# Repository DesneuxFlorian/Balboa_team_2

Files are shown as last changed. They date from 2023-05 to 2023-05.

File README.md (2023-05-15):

# Balboa_team_2
Advanced control 2 balboa robot
As part of the Advanced control 2 course, we did a job in which we were able to choose our own subject with the mobile balboa robot. We opted for subject number 6 "SLAM ROBOT". This subject consists in creating a map of an unknown environment thanks to the remote control of our laptop. The purpose of this documentation is to understand how to reproduce our project and then improve it for the years to come.

Vidéo to project: https://www.youtube.com/watch?v=urFcWSqZmxI

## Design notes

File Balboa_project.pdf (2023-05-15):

# 5/15/2023 Advanced control 2:

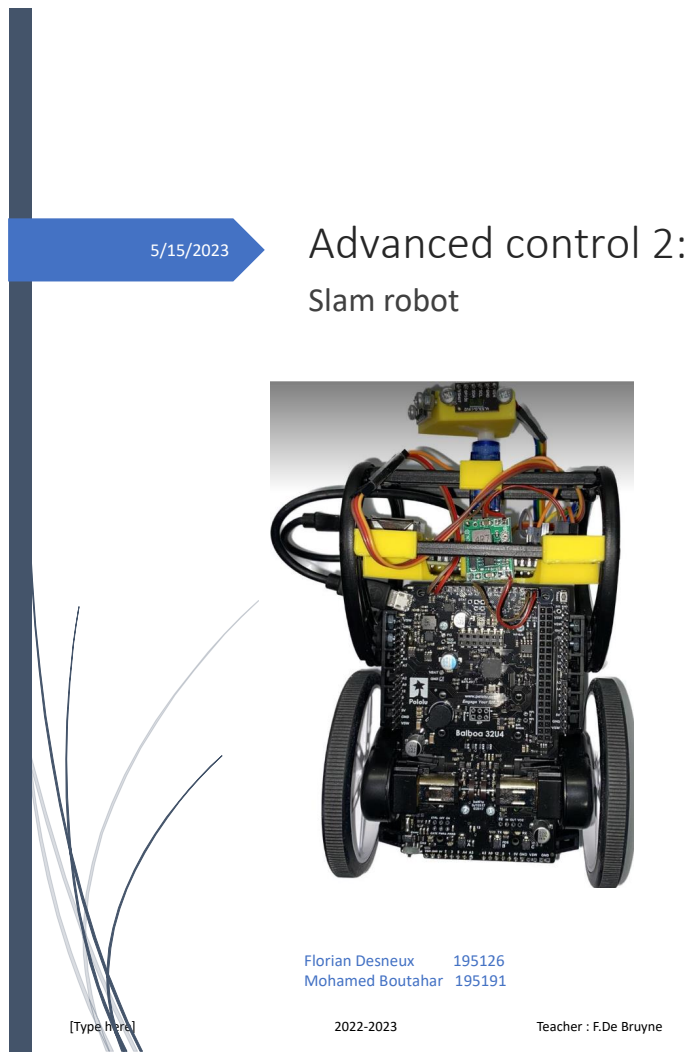
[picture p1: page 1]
[Type here]; Teacher : F.De Bruyne; Slam robot; Florian Desneux; Mohamed Boutahar 195191

## Contents

## 1. Project introduction

As part of the Advanced control 2 course, we did a job in which we were able to choose our own subject with the mobile balboa robot. We opted for subject number 6 "SLAM ROBOT". This subject consists in creating a map of an unknown environment thanks to the remote control of our laptop. The purpose of this documentation is to understand how to reproduce our project and then improve it for the years to come. If you are interested in the details and source files for this project, please follow this link to the project github : https://github.com/DesneuxFlorian/Balboa_team_2

## 2. Objectives

In order to carry out this project as well as possible, we have set ourselves several objectives which are as follows :

- Laser sensor with servo-motor
- Data collected and sended to laptop with mqtt
- Laptop controls the robot with user input
- Basic odometry data computed and sended to the laptop
- Implement a SLAM algorithm

## 3. Raspberry pi Setup

For the project we are using a raspberry pi as the main computer. It will be in charge of the communication between the Balboa and the Laptop. Additionally, the Raspberry will be operating the lidar scanner. We used this approach to try to run a SLAM algorithm on the raspberry.

### 3.1 OS installation

The first step is to install a Linux OS on the raspberry pi. For this we used this tutorial: How to Install Raspberry Pi OS on Your Raspberry Pi. (https://howchoo.com/pi/install-raspberry-pi-os) Because we will want to use remote access to the Raspberry using SSH, we need to add the following step during the installation:

1. Go to additional Settings.
2. Be sure to enable SSH.
3. Put a username and password that you will remember.
4. You can also set the hostname you want, it will become handy later on.
5. Enable and configure your wi-fi settings in the W-lan tab.

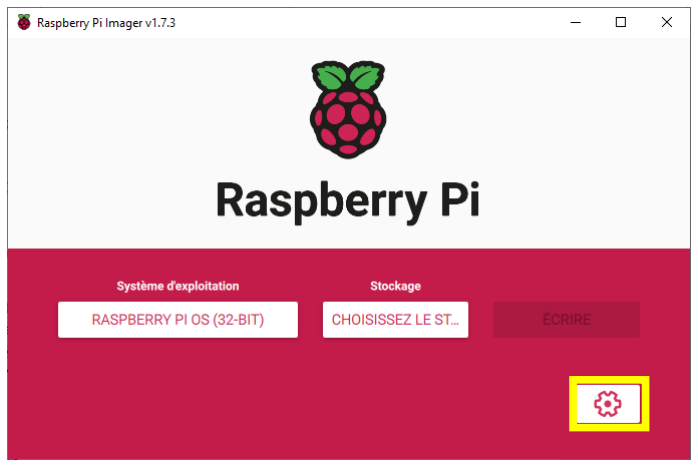
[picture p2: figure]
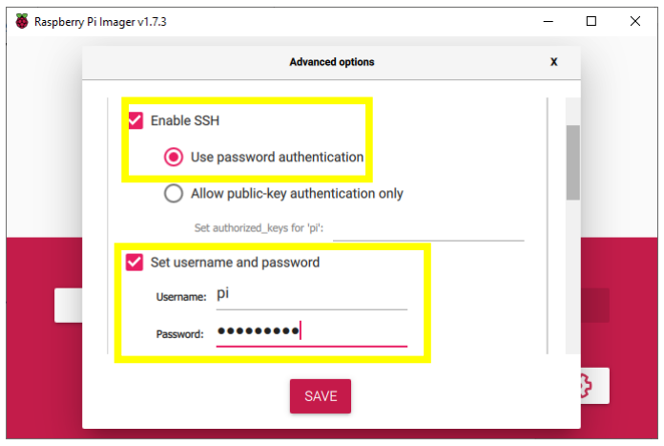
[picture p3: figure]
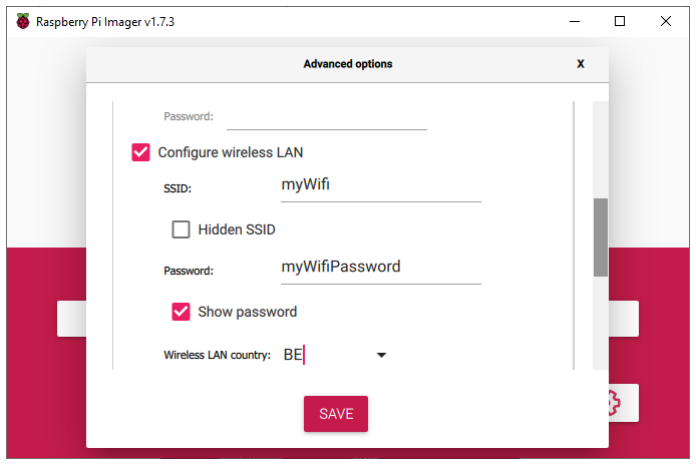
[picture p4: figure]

Save and write the OS to your SD card. You should then be able to boot the raspberry pi.

### 3.2 VNC setup

It is now time to connect via SSH to our raspberry pi. Once that is working, we will install a VNC viewer to access a remote desktop. To access via SSH, we need to know the IP address of the raspberry pi on the current network. To do this, we need to boot the raspberry with the SD card we just configured. When it is done booting (could take a minute or two), we need to find the IP address that has been assigned to the raspberry pi. There are several ways to find the IP address. This tutorial will show different ways to do that: How to Find a Raspberry Pi on a Network. (https://all3dp.com/2/find-raspberry-pi-on-network/) We used the third approach with a windows terminal and using ping command. The hostname of the raspberry pi is the hostname you have configured earlier. You should get an IP address of the type 192.XXX.X.XX. If you get an address with another format, use this one, but you will have to find the IP address once you are connected because VNC viewer only supports the first format.

A second way of finding the IP address remotely is to connect to your router’s login page. Most internet providers allow you to oversee all the connected devices on your network and you should be able to find the IP address of every connected device, including your Raspberry pi. If you cannot find your raspberry pi, it is possible it isn’t connecting properly to your network. Follow the troubleshooting steps of the tutorial to try to find your problem.

We can now test to connect via SSH to the raspberry pi before moving on to the next step. On windows open a command terminal and use the command: ssh pi@192.XXX.X.XX replacing “192.XXX.X.XX” with your raspberry IP address. Enter your password and you should be connected to the raspberry. If you got a IP address of the other type, we need to get the real IP address of the raspberry pi for the VNC viewer. Use the command sudo hostname -I in the command terminal to find it.

You can now install Real VNC (https://www.realvnc.com/fr/connect/download/viewer/) and connect to the pi using it’s IP address. You should get access to the raspberry pi desktop.

### 3.3 MQTT Setup

To communicate with the laptop, our code will use MQTT. So we need to install mosquito on the raspberry pi. We have followed this tutorial enabling remote access without authentication: Install Mosquitto MQTT Broker on Raspberry Pi. (https://randomnerdtutorials.com/how-to-install-mosquitto-broker-on-raspberry-pi/) We also need to install the python package to use mosquito with python. Open a terminal and run pip3 install paho-mqtt.

### 3.4 Additional dependencies Setup

The code is using some other packages. Here is a list of the packages you should install on python3:

− numpy
− serial
− smbus2
− vl53l1x
− json

Install all of these dependencies using PIP3.

Finally you should also go to the configuration tab of the pi and enable i2c, Serial port and VNC. Don’t forget to reboot the pi after changing the configuration (command sudo reboot).

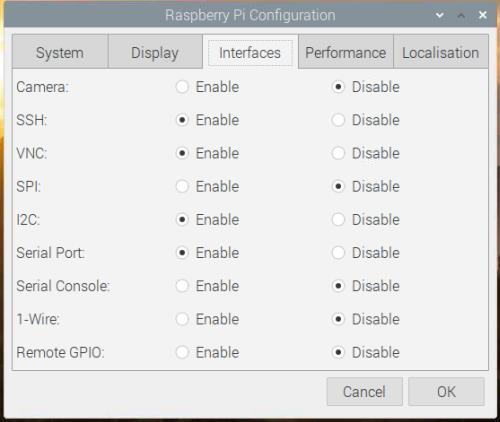
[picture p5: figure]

### 3.5 Hotspot tools V2

We also want to install hotspot tools v2 on our raspberry pi. This way we will be able to control the robot event when there is no available wifi network. The raspberry will boot in a hotspot mode and we then simply need to connect to its local network. This will also enable us to setup new wifi connections without needing to restart the other steps. To install hotspot tools v2 we simply followed the steps for installing from the project Github page¹
| . There is also a video available for a more in depth tutorial.

## 4. Communication between balboa robot and raspberry PI

Here, we will communicate in series between the balboa and the Raspberry PI thanks to a USB cable connecting the balboa robot to one of the USB ports of the Raspberry Pi.

### 4.1 Serial communication

The principle of serial communication is to sequentially send one bit of data at a time from one location to another. For example, using serial data, you can send data from your balboa to a Raspberry Pi or from the Raspberry Pi to the balboa.

After discussing with our teacher, we chose to communicate with a USB cable because it is one of the most common ways to transmit data in serial communications hence the name of universal serial bus. So with balboa, we can easily send and receive data via a USB cable thanks to balboa's built-in serial library.

### 4.2 UART communication

Once the data has arrived on our balboa, it will be stored in what we call "serial reception buffer".

1 https://github.com/km4ack/hotspot-tools2

When bits of data start flowing into the computer, a hardware device in the balboa used for serial communication between two devices called a universal asynchronous receiver/transmitter (UART) assembles each of the 8 bits into a byte. The UART then stores these bytes (up to 64 bytes, in fact) in the serial receive buffer.

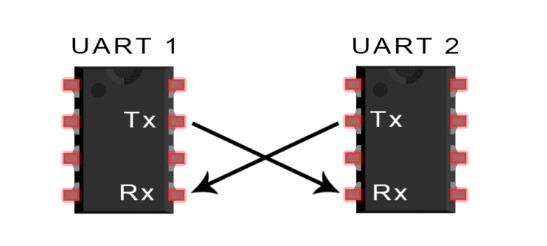
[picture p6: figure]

One wire is for transmitting data (called the TX pin) and the other is for receiving data (called the RX pin). We can only connect two UART devices together.

Once the data is in the serial receive buffer, we can use Serial.read() to read what is in the receive buffer. However, it’s important to understand that it reads in a very specific way. It’ll read out the first available byte from the serial receive buffer and then remove that byte from the buffer.

In order to simplify things, we will impose a rather basic protocol :

- New messages will be read as soon as they arrive
- Messages must not exceed 12 bytes
- Each message will end with a newline character '\n' which we will call our end character

## 5. Communication between Raspberry pi and laptop

We are using 3 different topics for the communication.

1. raspberry/scan
2. raspberry/odom
3. raspberry/setpoint

The first and second topics are published on with the raspberry pi, and the third topic is used to control the balboa from the laptop. It is published on when you press a key controlling the robot. We are using keys “i,j,k,l” to move the robot around, key “t” to start and stop the scanning and finally you can use key “s” to save the data coming from the robot.

## 6. Electrical circuit

Here we will illustrate in detail the wiring of our project

### 6.1 Power supply of the raspberry PI

Regarding the power supply of the raspberry PI, we decided to power it directly with the balboa. The problem is that our raspberry PI has to be powered with 5 V while our balboa provides a battery voltage. To solve this problem, we decided to use a buck converter to reduce this voltage to 5 V. Here is the buck we decided to use:

By using the buck converter, we are sure that there is enough power for the raspberry pi. Normally the balboa already has a 5v bus that we could use, but it was not powerful enough and that’s why we made the choice to use a buck converter.

### 6.2 Servomotor

In order to have a maximum of data to better map the environment, we decided to mount our sensors on a servomotor which will turn it at a certain angle.

### 6.3 Wiring diagrams

Here is a complete assembly of our balboa robot with the different elements such as the buck, the servomotor, the sensors and the raspberry PI

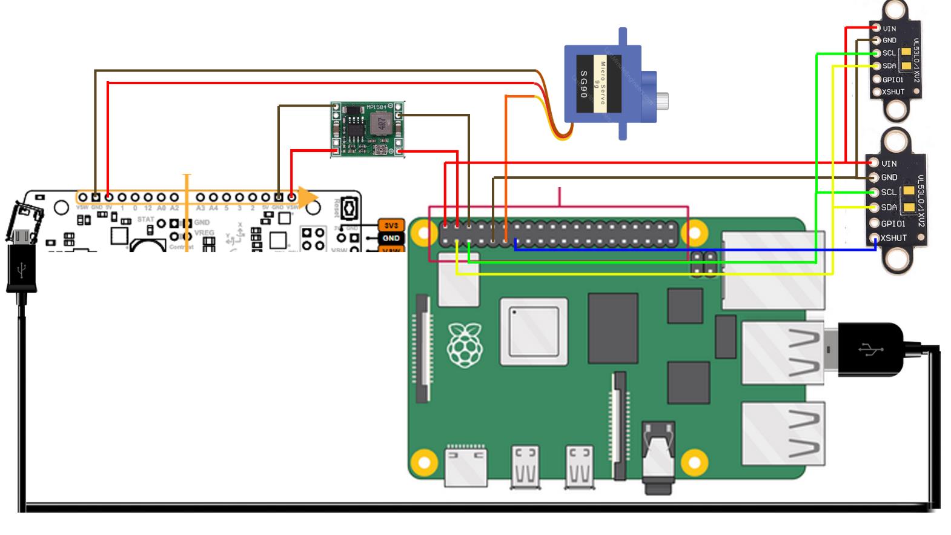
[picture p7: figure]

## 7. Software

The software is composed of three big parts. The first part is the C++ code running on the Balboa robot itself. Basically it is in charge of the control algorithm as well as computing the dead reckoning odometry for the robot. The second part of code is the python code running directly on the raspberry pi. This part of the code is responsible for controlling the lidar scanner, and sending the data to the laptop. It is also used as middleman for controlling the balboa with the laptop. The raspberry pi gets control commands from the laptop trough MQTT, and then sends them to the balboa trough serial. The last part of code is also a python code that is running on the laptop. Its purpose is to retrieve keyboard commands and send them to the raspberry and to receive the scanned data from the raspberry pi and to display them on the screen. It is also in this code that we convert the data from polar to cartesian.

### 7.1 Balboa code

The control is performed by a state-space algorithm. Additionally we have added a few functions:

− ComputeOdom()
− readData()
− treatCommand()
− sendOdometry()

The ComputeOdom function is running every 10ms to evaluate the balboa robot position in a cartesian coordinate system. It is implemented following this article found online²
. The second
and third functions are running at a much higher sampling rate than the rest of the control algorithm. This ensure that a fast serial communication between the raspberry and the balboa as well as a fast handling of the commands. The last function is simply sending the odometry data trough serial when the robot reads a “O” in the serial buffer.

### 7.2 raspberry pi code

The code running on the raspberry pi is composed of 2 files. The Lidar file, that contains a Lidar class. This class is in charge of everything related to the laser scanners. It will connect to the two lidars, then it will start those lidars and finally it has a method to run a scan with the lidars. This class also controls the servo motor on which the two vl53l1x are mounted. The method performing the scan is working this way:

− first it moves the servo to a position
− then it asks the odometry to the Arduino
− get the distance from the two sensors
− appends the angles and distances to a list and performs everything for a new position − finally it returns the lists when the sweep is done

2 Wheel Odometry Model for Differential Drive Robotics (https://medium.com/@nahmed3536/wheel-odometry-model-for-differential-drive-robotics-91b85a012299)

Initially we were not getting the odometry for every point in the scan but only for the last one. It had the advantage to speed up the control of the balboa because it had less communication. But because the slow nature of our scan, it is a lot better to get the odometry for every point so that we can correct the list of angle for every point individually.

The second file is the main file. This file is the one that will be started and running continuously on the raspberry pi. It has a functions that handle the MQTT communication, as well as a main loop running where it will scan around using the lidar object created at the beginning of the code. Before running this file it is important to run the command “sudo pigpiod” in a command terminal so that the lidar class can correctly run. This class is using hardware pwm to control the servo motor. This is so to remove the jitter that we have if we use the conventional software generated pwm.

### 7.3 laptop code

Finally the code running on your laptop is composed of 3 files. The roboviz.py file is a file from the roboviz library written by Simond Levy³
. It has been slightly modified so for better result it is advised to use the file from this project github page. The lidar_to_grid_map.py file is a python file written by Erno Horvath⁴
| . This file has also been modified, thus the file from our github should also
be used to ensure that the code will run. Before running those files you should also check that you have installed the required dependencies on your laptop. For the laptop the dependencies are:
| − numpy − matplotlib − json − paho mqtt − keyboard

## 8. Mechanical assembly

Two 3D printed parts are used to mount the raspberry pi and the servo motor on top of the balboa robot. Those 3d prints simply clip on the already existing mounts. There is also a small 3d printed support to mount the two VL53L1X on the 8g servo motor.

## 9. Results and improvements ideas

The robot is performing quiet well. When it is not scanning around it is easy to drive it around to where we want it to go. But because our scanner is slow we are controlling it with slow values. To start scanning we simply push on “t” on the keyboard. As soon as it starts scanning, there is a noticeable loss of control from the pc. The balboa is less reactive to keyboard commands. This comes from the increased communication from the odometry data. As we drive it around we can slowly see a map displaying on our screen. But because we don’t run a real SLAM algorithm, the map is quickly becoming bad as a result of the odometry drift. The images below show some maps that we could draw.

3 https://github.com/simondlevy/PyRoboViz
4 https://github.com/AtsushiSakai/PythonRobotics/tree/master/Mapping/lidar_to_grid_map

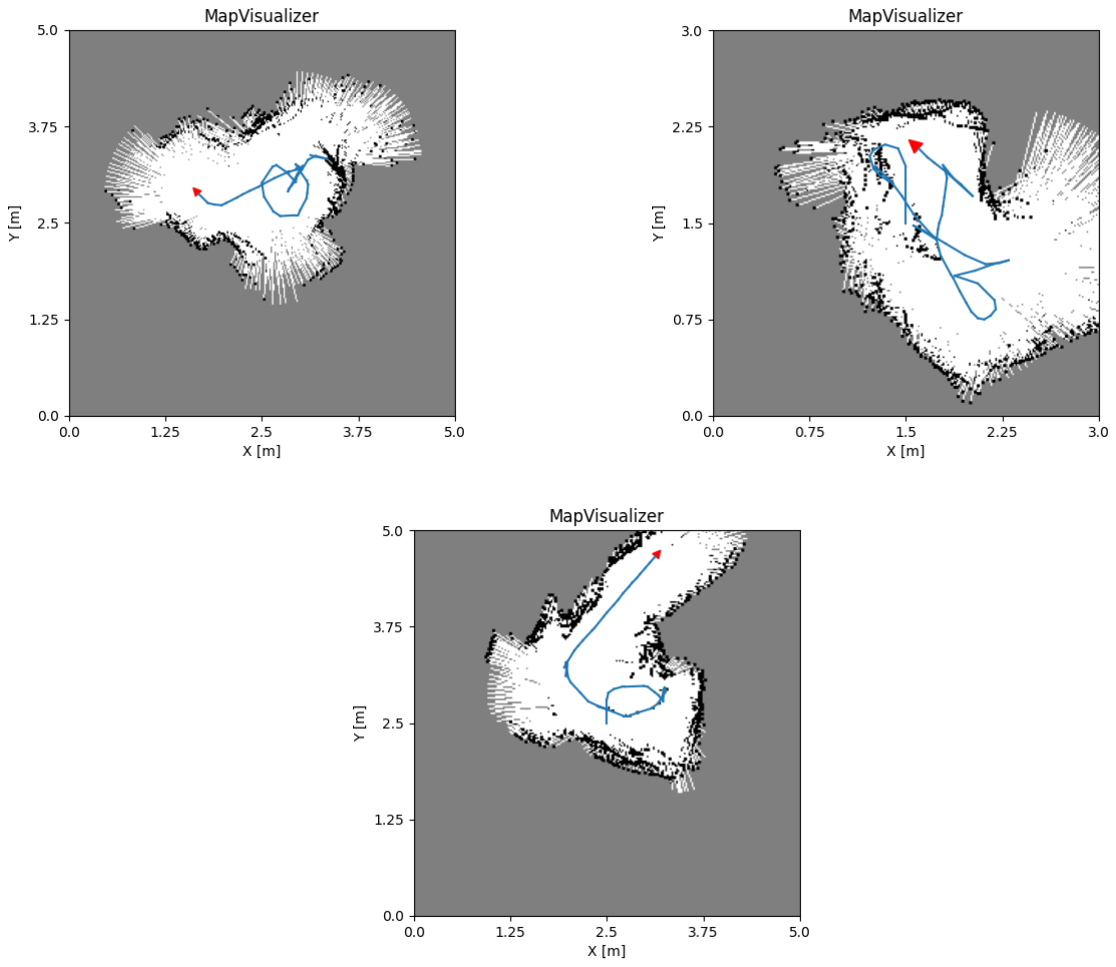
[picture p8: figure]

On the maps we can see that on some places data overlaps or that there are scans of the same feature but a different places.

To improve our robot there are several ideas we could try to implement.

The first idea we have is to change the scanner with a scanner with a much higher sampling rate. Something around 5 scans/s should be enough. This improvement would help with a few problems we had. Firstly we could remove the need to correct every point of the scan with the robot odometry. This would reduce the amount of serial communication and thus the control of the robot would be the same as when we are not scanning, so a lot better. Secondly with a faster and better scanner we could try to implement a real SLAM algorithm. This was impossible with the data from our scanner. This would mostly solve the drift problem from the odometry data. If we change the scanner we would be able to really use the robot to map its environment and even try to do some path planning. A good replacement scanner that could be used as a starting point is the openSimpleLidar project from iliasem⁵
. This lidar could maybe be redesigned to be smaller and lighter to work on the balboa robot.

5 https://github.com/iliasam/OpenSimpleLidar

A second idea to improve the robot is to use the magnetometer as a reference point for the balboa heading in the odometry. We tried to use it, but the balboa is known to have hard and soft iron problems, making the data from the magnetometer hard to use. Even when performing a 3d calibration as explained here (https://forum.pololu.com/t/correcting-the-balboa-magnetometer/14315) it was only giving good result for some amount of time. When using the same calibration somewhere else or later at the same location the results were not good as initially. Maybe it is possible to perform a calibration and use the raspberry pi to compute the correction coefficient at every startup of the robot.

Finally we thought about using ROS on the raspberry pi. By using micro-ROS on the balboa we should be able to use ROS to control the balboa and so every ROS feature, including the mapping and path planning algorithms could be used to improve this project.

## 10. Conclusion

In conclusion, we have achieved all our objectives mentioned in point 2 except the last one which is the implementation of the slam algorithm. To achieve this one we should try to improve our robot with the ideas explained before.

## 11. References

Configure the raspberry

https://howchoo.com/pi/install-raspberry-pi-os

https://howchoo.com/g/ndy1zte2yjn/how-to-set-up-wifi-on-your-raspberry-pi-without-ethernet

https://all3dp.com/2/find-raspberry-pi-on-network/

Communication part

Serial.read and Arduino: Here's the advanced stuff you should know (programmingelectronics.com) (https://www.programmingelectronics.com/serial-read/)

How to Set Up UART Communication on the Arduino - Circuit Basics (https://www.circuitbasics.com/how-to-set-up-uart-communication-for-arduino/)

https://www.instructables.com/Installing-MQTT-BrokerMosquitto-on-Raspberry-Pi/

Other

https://github.com/km4ack/hotspot-tools2

https://forum.pololu.com/t/correcting-the-balboa-magnetometer/14315

https://github.com/iliasam/OpenSimpleLidar

https://gpiozero.readthedocs.io/en/stable/api_pins.html#changing-pin-factory

https://gpiozero.readthedocs.io/en/stable/api_output.html?highlight=Servo#gpiozero.Servo

https://github.com/AtsushiSakai/PythonRobotics/tree/master/Mapping

https://www.domo-blog.fr/comment-creer-un-serveur-mqtt-sur-le-raspberry-pi-avec-mosquitto/

https://www.youtube.com/watch?v=_fdwE4EznYo&t=706s

https://stackoverflow.com/questions/64642122/how-to-send-real-time-sensor-data-to-pc-from-raspberry-pi-zero (https://stackoverflow.com/questions/64642122/how-to-send-real-time-sensor-data-to-pc-from-raspberry-pi-zero)

https://roboticsbackend.com/raspberry-pi-arduino-serial-communication/

https://github.com/pimoroni/vl53l1x-python

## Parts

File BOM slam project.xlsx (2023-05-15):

NAME | LINK | NOTE | QUANTITY | UNIT PRICE | TOTAL PRICE
balboa 32u4 | https://www.pololu.com/category/210/balboa-robot-and-accessories |  | 1 | 90.00 € | 90.00 €
Raspberry pi 4 model B 4GB | https://shop.mchobby.be/fr/raspberry-pi-4/1610-raspberry-pi-4-4-go-de-ram-dispo-en-stock--3232100016101.html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 | difficult to source | 1 | 73.00 € | 73.00 €
9g servo motor | https://nl.banggood.com/SG90-Mini-Gear-Micro-Servo-9g-For-RC-Airplane-Helicopter-2pcs-p-1621423.html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 |  | 1 | 3.63 € | 3.63 €
VL53L1X | https://fr.aliexpress.com/item/4000049438709.html |  | 2 | 4.62 € | 9.24 €
DC-DC MP1584EN | https://www.amazon.fr/gp/product/B07DJ5HZ7G/ref=ox_sc_act_title_1?smid=A3SCFTIO8CSK1X&psc=1 |  | 1 | 1.80 € | 1.80 €
 |  |  |  |  | 0.00 €
 |  |  |  |  | 0.00 €
Total |  |  |  |  | 177.67 €

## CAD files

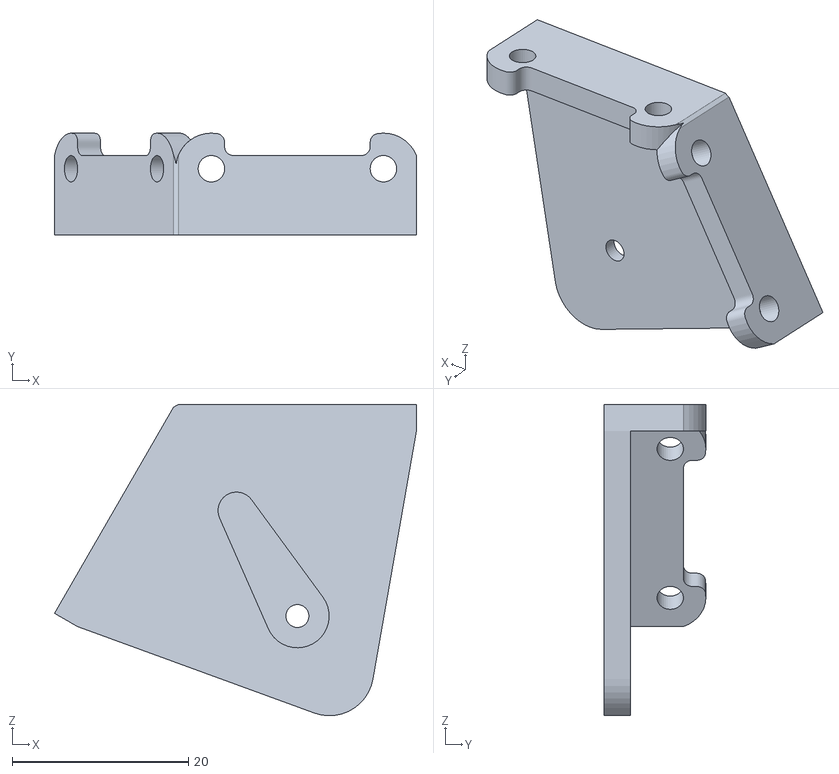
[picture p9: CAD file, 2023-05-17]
3D_prints/Scanner.STL
41.0 x 11.5 x 35.3

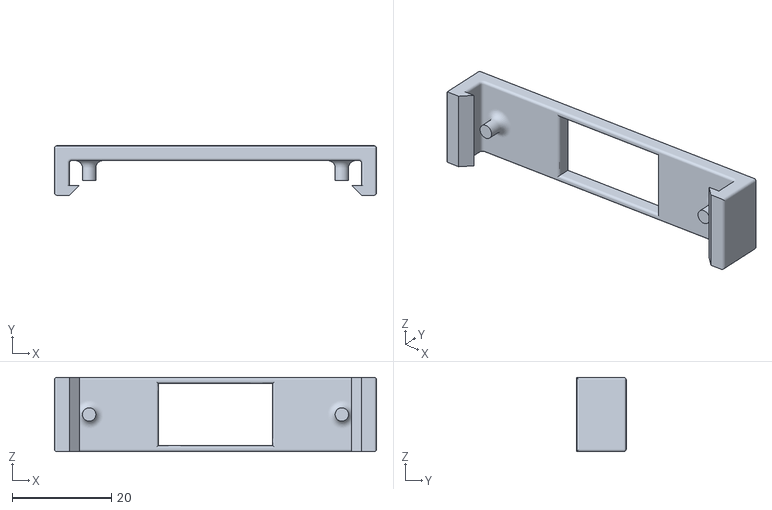
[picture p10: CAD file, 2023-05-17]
3D_prints/Servo_Holder.STL
65.0 x 10.0 x 15.0

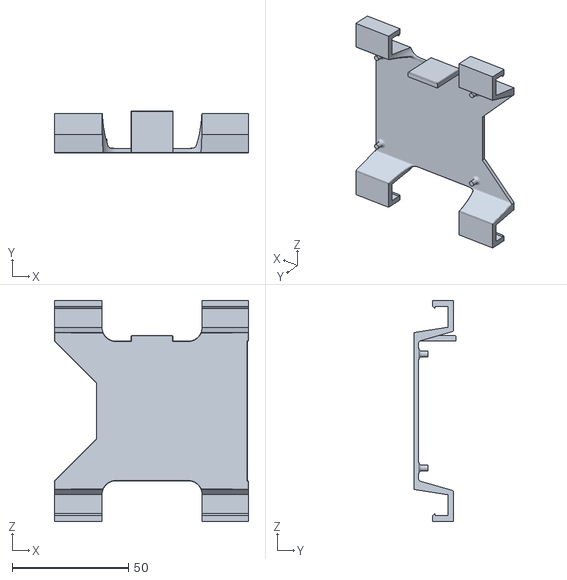
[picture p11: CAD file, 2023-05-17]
3D_prints/Pi_Holder.STL
83.5 x 18.0 x 95.0

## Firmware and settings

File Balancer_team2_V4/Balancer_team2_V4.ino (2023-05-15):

// This example shows how to make a Balboa balance on its two
// wheels and drive around while balancing.
//
// To run this demo, you will need to install the LSM6 library:
//
// https://github.com/pololu/lsm6-arduino
//
// To use this demo, place the robot on the ground with the
// circuit board facing up, and then turn it on.  Be careful to
// not move the robot for a few seconds after powering it on,
// because that is when the gyro is calibrated.  During the gyro
// calibration, the red LED is lit.  After the red LED turns off,
// turn the robot so that it is standing up.  It will detect that
// you have turned it and start balancing.
//
// Alternatively, you can press the A button while the robot is
// lying down and it will try to use its motors to kick up into
// the balancing position.
//
// This demo is tuned for the 50:1 high-power gearmotor with
// carbon brushes, 45:21 plastic gears, and 80mm wheels; you will
// need to adjust the parameters in Balance.h for your robot.
//
// After you have gotten the robot balance well, you can
// uncomment some lines in loop() to make it drive around and
// play a song.

#include <Balboa32U4.h>
#include <Wire.h>
#include <LSM6.h>
#include <LIS3MDL.h>
#include "Balance.h"
LSM6 imu;
LIS3MDL mag;
Balboa32U4Motors motors;
Balboa32U4Encoders encoders;
Balboa32U4Buzzer buzzer;
Balboa32U4ButtonA buttonA;
Balboa32U4ButtonB buttonB;
Balboa32U4ButtonC buttonC;
long rana;


void setup()
{
  // Uncomment these lines if your motors are reversed.
  // motors.flipLeftMotor(true);
  // motors.flipRightMotor(true);

  ledYellow(0);
  ledRed(1);
  balanceSetup();
  ledRed(0);
  randomSeed(134);

}

const char song[] PROGMEM =
  "!O6 T240"
  "l32ab-b>cl8r br b-bb-a a-r gr g-4 g4"
  "a-r gr g-gg-f er e-r d4 e-4"
  "gr msd8d8ml d-4d4"
  "l32efg-gl8r msd8d8ml d-4d4"
  "<bcd-d e-efg- ga-ab- a4 gr";

void playSong()
{
  if (!buzzer.isPlaying())
  {
    buzzer.playFromProgramSpace(song);
  }
}

void driveAround()
{
  uint16_t time = millis() % 2048;
  uint16_t leftSpeed, rightSpeed;
  if (time < 1000)
  {
    leftSpeed = 10;
    rightSpeed = 10;
  }
  else if (time <1024)
  {
    rana =random(-1000,1000);
    
  }
  else if (time < 1024+abs(rana))
  {
    if (rana>0)
    {
    leftSpeed = 5;
    rightSpeed = -5;
    }else{
    leftSpeed = -5;
    rightSpeed = 5;
    }
  }
  else
  {
    leftSpeed = 3;
    rightSpeed = 3;
  }

  balanceDrive(leftSpeed, rightSpeed);
}

void standUp()
{
  motors.setSpeeds(0, 0);
  buzzer.play("!>grms>g16>g16>g2");
  ledGreen(1);
  ledRed(1);
  ledYellow(1);
  while (buzzer.isPlaying());
  motors.setSpeeds(-MOTOR_SPEED_LIMIT, -MOTOR_SPEED_LIMIT);
  delay(250);
  motors.setSpeeds(300, 300);
  for (uint8_t i = 0; i < 150; i++)
  {
    delay(UPDATE_TIME_MS);
    balanceUpdateSensors();
    if(angle < 60000)
    {
      break;
    }
  }
  motorSpeed = 150;
  balanceResetEncoders();
}










void loop()
{
  static bool enableSong = false;
  static bool enableDrive = false;

  balanceUpdate();

  if (isBalancing())
  {
    if (enableSong)   { playSong(); }
    if (enableDrive)  { driveAround(); }
    Drive();//Drive balboa at higher sampling speed than the control algorithm
  }
  else
  {
    buzzer.stopPlaying();
    balanceDrive(0, 0); // reset driving speeds

    if (buttonA.getSingleDebouncedPress())
    {
      enableSong = false;
      enableDrive = true;
      standUp();
    }
    else if (buttonB.getSingleDebouncedPress())
    {
      enableSong = false;
      enableDrive = true;
      standUp();
    }
    else if (buttonC.getSingleDebouncedPress())
    {
      enableSong = true;
      enableDrive = true;
      standUp();
    }
  }
  
  if(Serial.available()>0){
    readData();
  }
  // Illuminate the red LED if the last full update was too slow.
  ledRed(balanceUpdateDelayed());

  // Display feedback on the yellow and green LEDs depending on
  // the variable fallingAngleOffset.  This variable is similar
  // to the risingAngleOffset used in Balance.cpp.
  //
  // When the robot is rising toward vertical (not falling),
  // angleRate and angle have opposite signs, so this variable
  // will just be positive or negative depending on which side of
  // vertical it is on.
  //
  // When the robot is falling, the variable measures how far off
  // it is from a trajectory starting it almost perfectly
  // balanced then falling to one side or the other with the
  // motors off.
  //
  // Since this depends on ANGLE_RATE_RATIO, it is useful for
  // calibration.  If you have changed the wheels or added weight
  // to your robot, you can try checking these items, with the
  // motor power OFF (powered by USB):
  //
  // 1. Try letting the robot fall with the Balboa 32U4 PCB up.
  //    The green LED should remain lit the entire time.  If it
  //    sometimes shows yellow instead of green, reduce
  //    ANGLE_RATE_RATIO.
  //
  // 2. If it is tilted beyond vertical and given a push back to
  //    the PCB-up side again, the yellow LED should remain lit
  //    until it hits the ground.  If you see green, increase
  //    ANGLE_RATE_RATIO.
  //
  // In practice, it is hard to achieve both 1 and 2 perfectly,
  // but if you can get close, your constant will probably be
  // good enough for balancing.
  // int32_t fallingAngleOffset = angleRate * ANGLE_RATE_RATIO - angle;
  // if (fallingAngleOffset > 0)
  // {
  //   ledYellow(1);
  //   ledGreen(0);
  // }
  // else
  // {
  //   ledYellow(0);
  //   ledGreen(1);
  // }
}

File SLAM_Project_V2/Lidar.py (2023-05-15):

import RPi.GPIO as GPIO
import VL53L1X
import argparse
import time
import numpy as np
from gpiozero import Servo
from gpiozero.pins.pigpio import PiGPIOFactory

def auto_int(x):
	return int(x, 0)

class Lidar:
	

	
	def __init__(self,servo_Pin,Xshut_pin,addr,arduinoDevice):
		self.arduino=arduinoDevice
		self.Xshut_pin=Xshut_pin
		self.address_Second_Sensor=addr
		
		GPIO.setmode(GPIO.BCM) #set gpio mode, set xshutpin of one sensor to
		GPIO.setup(Xshut_pin,GPIO.OUT)#LOW to shut it down and change address 
		
		GPIO.output(Xshut_pin,GPIO.LOW)#of the other sensor
		#change address of second sensor to 0x30
		self.__change_Address(0x29,self.address_Second_Sensor)
		
		GPIO.output(Xshut_pin,GPIO.HIGH)#turn back on sensor
		self.tof=VL53L1X.VL53L1X(i2c_bus=1, i2c_address=0x29)
		self.tof2=VL53L1X.VL53L1X(i2c_bus=1, i2c_address=self.address_Second_Sensor)
		self.tof.open()
		self.tof2.open()
		
		
		#setup servo motor
		factory=PiGPIOFactory()
		self.servo=Servo(servo_Pin,min_pulse_width=0.5/1000,max_pulse_width=2.5/1000,pin_factory=factory)
		

		
		self.servo_Angle=-90
		self.servo.value=-1/3 #set servo to start postion
		time.sleep(1)
		self.rightPos=True
		
		
	def start(self,distance_Mode,Timing_Budget,Intermeasurement_Time):
		self.tof.set_timing(Intermeasurement_Time, Timing_Budget)
		self.tof2.set_timing(Intermeasurement_Time, Timing_Budget)
		self.tof.start_ranging(distance_Mode)
		self.tof2.start_ranging(distance_Mode)
		
	
	def stop(self):
		self.tof.stop_ranging()
		self.tof2.stop_ranging()
		self.tof.close()
		GPIO.output(self.Xshut_pin,GPIO.LOW)#reset second sensor to default address
		self.tof2.close()
		self.__change_Address(self.address_Second_Sensor,0x29)
		GPIO.output(self.Xshut_pin,GPIO.HIGH)
	
	
	def scan_Around(self,angle,n):
		maxRange=1200 #mm
		self._angleScan=np.empty(0)
		self._distanceScan=np.empty(0)
		
		if self.rightPos:#right to left
			for self.servo_Angle in range(0,n):
				self.servo.value=(angle)/180-1+self.servo_Angle*(angle/n)/180
				x,y,angle_rob=self.getOdom()
				#print(angle)
				distance_mm=self.tof.get_distance()
				distance_mm2=self.tof2.get_distance()
				if distance_mm>maxRange:#rescale to max if distance is greater than the maxRange
					distance_mm=maxRange
				if distance_mm2>maxRange:
					distance_mm2=maxRange
				self._distanceScan=np.append(self._distanceScan,[distance_mm,distance_mm2])
				self._angleScan=np.append(self._angleScan,np.round([self.servo.value*180/2+60+angle_rob,self.servo.value*180/2+120+angle_rob],2))#,self.servo.value*180+150
				self.rightPos=False
			#time.sleep(0.1)
		else:#left to right
			for self.servo_Angle in range(1,n+1):
				self.servo.value=-((angle)/180-1)-self.servo_Angle*(angle/n)/180
				x,y,angle_rob=self.getOdom()
				distance_mm=self.tof.get_distance()
				distance_mm2=self.tof2.get_distance()
				if distance_mm>maxRange:#rescale to max if distance is greater than the maxRange
					distance_mm=maxRange
				if distance_mm2>maxRange:
					distance_mm2=maxRange
				self._distanceScan=np.append(self._distanceScan,[distance_mm,distance_mm2])
				self._angleScan=np.append(self._angleScan,np.round([self.servo.value*180/2+60+angle_rob,self.servo.value*180/2+120+angle_rob],2))
				self.rightPos=True
		return self._angleScan,self._distanceScan	
		
		
	def __change_Address(self,addr_current,New_address):
		tof = VL53L1X.VL53L1X(i2c_bus=1, i2c_address=addr_current)
		tof.open()
		tof.change_address(New_address)
		tof.close()
		
	
	def getOdom(self):
		try:
			msg="O\n"
			self.arduino.write(msg.encode())
			time.sleep(0.01)
			if self.arduino.in_waiting>0:
				bytesRead=self.arduino.readline()
				odom=bytesRead.decode('utf-8')
				odom=odom.split(";")
				x=int(odom[0])*10# mm
				y=int(odom[1])*10# mm
				yaw=np.rad2deg(int(odom[2])/1000.0)# deg
				return x,y,yaw
			
		except:
			print("error_odom")
			return 0,0,0

if __name__=="__main__":

	test=Lidar(13,0x30)
	test.start(1)

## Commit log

2023-03-03 Add files via upload
    main python file and Lidar class
2023-04-27 Add files via upload
    balboa state space without reduced observer
    mqtt visualisation of data send by raspberry pi
2023-05-15 Add files via upload
    final raspberry pi code
